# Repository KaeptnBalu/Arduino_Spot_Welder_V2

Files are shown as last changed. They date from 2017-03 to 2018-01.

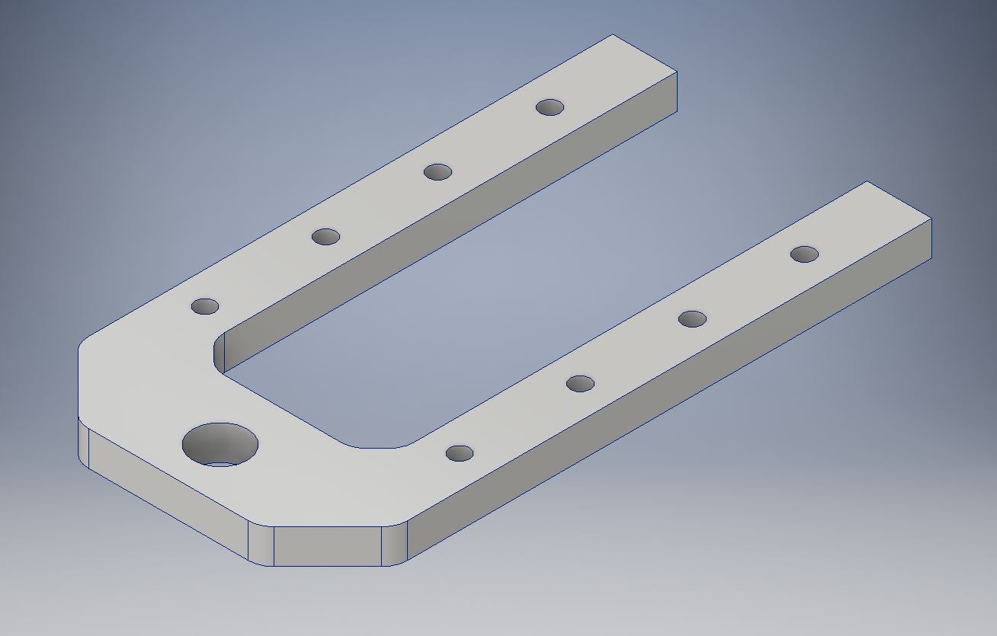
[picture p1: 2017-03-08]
Parts/Aluminum_Parts/Part1_new.JPG

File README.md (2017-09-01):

# Arduino_Spot_Welder_V2

This is the older V2 Version of the Arduino Spot Welder. The new V3 can be found here https://github.com/KaeptnBalu/Arduino_Spot_Welder_V3 The previous V1 can be found here https://github.com/KaeptnBalu/Arduino_Spot_Welder

An Arduino based Spot Welder for battery welding http://www.instructables.com/id/DIY-Arduino-Battery-Spot-Welder/ <br>
Build Video: https://www.youtube.com/watch?v=4qOaeutVR8I

3D prinable cases: 
- https://www.thingiverse.com/thing:2488481   (Thanks to Neil Paisnel)
- https://www.thingiverse.com/thing:2346476   (Thanks to AugustRetroDoom)

Improvements in the V2:

    - only one mosfet driver instead of four
    - changed electrolytic capacitor to film capacitor
    - capacitors closer to the mosfet driver
    - wider pcb traces for high current paths
    - added gate resistors for the mosfets
    - aluminum u-shaped part for the mosfet board (much easier to assemble)
    - general pcb layout improvements
    - pcb is now designed in KiCad (more open source than Eagle)
    
 Improvements in the V2.2:

    - Mosfet PCB now with 2oz copper layer and wider traces 
    which connect the high current carrying mosfet legs to the u-shaped aluminum part
    - little bit bigger mounting holes for u-shaped aluminum piece (2.6mm instead of 2.5mm)
    - "AutoPulse" feature, which automatically activates a pulse after a 2 second delay 
    when both welding tips touch the nickel strip (thanks to Petr Zverina for the idea)

This Spot Welder can be used to weld 18650 batteries. It needs a 7-12V power source (12V recommended) and uses a 12V car battery as welding current supply. Typically one 45Ah battery delivers enough current to get good welds with 0.15mm nickel strips. For thicker nickel strips maybe you will need bigger battery or two in paralell.

The Welder generates a double pulse, where the first one is 1/8 of the time of the second one. Pulse time of second pulse is adjustable by the potentiometer and displayed on the screen in mS so you can exactly adjust the time. Its adjustable from 1 ... 90 mS.

If you want to download the project click on "clone or download" on this page. Downloading single files sometimes seems to cause some files to be corrupted while downloading.

You can get parts to build your own Spot Welder or prebuilt kits at https://malectrics.eu/

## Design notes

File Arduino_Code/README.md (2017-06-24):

The code for the Spot welder V2 or V2.1 is the arduino_spot_welder.ino . The code for the new V2.2 PCBs with "AutoPulse" feature is the Arduino_Spot_Welder_V2.2.ino . Only use the new V2.2 code if you have the new V2.2 PCBs or if you upgraded your old Spot Welder with the necessary parts. 

If you built the spot welder yourself but it doesn't work, you can use the TEST_MODE_Arduino_Spot_Welder.ino to find the error. DO NOT CONNECT THE WELDING WIRES WHEN USING THIS CODE ! With the test code pushing the foot switch turns the mosfets permanent on. This way you can measure all the voltages with a normal multimeter. For example you can check:

- if all mosfet gates get the full voltage when they are on. They should have almost the voltage of your power supply.
- if the Arduino outputs a high signal (5V) to the mosfet drivers (Arduino Pin D5, Mosfet Driver Pin 2)
- if the LED gets a high signal (5V)

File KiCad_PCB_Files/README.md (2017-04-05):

The spot welder is made of two boards which are stacked on top of each other.
One board contains all the logic and low power electronic components and the other one contains the Mosfets.

The gerber files are made to be used at pcbway.com 
You can support me by registering through this link http://www.pcbway.com/setinvite.aspx?inviteid=12824
This way you get a 5$ coupon for your order and i get some percent discount at the shop for upcoming projects.

As the Gerber Files you can use the Spot_Welder_V2_Gerber.zip or the latest Spot_Welder_V2.1_Gerber.zip which have both boards combined to one big board. 
You have to cut this in half at home to get the two single boards.

To download the files please download the complete project by clicking on the "clone or download" button on the projects main page (https://github.com/KaeptnBalu/Arduino_Spot_Welder_V2)
Downloading by right click and "save as" does seem to cause problems.

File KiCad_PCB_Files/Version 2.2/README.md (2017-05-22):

Improvements in Version 2.2

- Mosfet PCB now with 2oz copper layer and wider traces which connect the high current carrying mosfet legs to the u-shaped aluminum part
- little bit bigger mounting holes for u-shaped aluminum piece (2.6mm instead of 2.5mm)
- "AutoPulse" feature, which automatically activates a pulse after a 2 second delay when both welding tips touch the nickel strip (thanks to Petr Zverina for the idea)

The mosfet pcb update was done because some users who tryed welding with more than 1000A current reported that the pcb traces got damaged by the high current. Now it should be more resistant even to these very high currents.

The new "AutoPulse" feature only needs 5 small additional parts on the pcb. (470 Ohm resistor, 620 Ohm resistor, z-diode 4,3V 0,5w, 2,54mm jumper, 2 pin 2,54mm male header). Resistor R13 does not need to be populated. It was meant as a pull down resistor, but after looking close to the schematic i realised R14 + R15 already do the pull down to GND.

To activate the "AutoPulse" feature simply plug a jumper on the male 2 pin header named "Auto_Pulse" which connects the two pins.

You can get the new V2.2 PCB Sets here: https://malectrics.eu/

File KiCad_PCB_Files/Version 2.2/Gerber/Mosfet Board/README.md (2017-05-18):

Gerber files to order the Mosfet Board at a pcb manufacturer

NOTE:
order the mosfet board with 2oz copper to make it able to handle welding currents of more than 1000A

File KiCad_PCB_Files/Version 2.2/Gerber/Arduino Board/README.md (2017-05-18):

Gerber Files to order the Arduino Board at a pcb manufacturer

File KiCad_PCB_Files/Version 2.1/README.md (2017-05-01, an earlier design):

These are the KICAD PCB Files for version 2.1 of the Arduino Spot Welder

Updates in V2.1:

- moved gnd_con text to bottom side
- moved mosfets pads 1mm to board outside
- larger smd pads for the led
- larger pin header pads
- capacitor 0,1µF and shottky diode now smd parts

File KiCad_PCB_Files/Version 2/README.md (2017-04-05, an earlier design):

These are the KICAD pcb files for the Arduino Spot Welder version 2

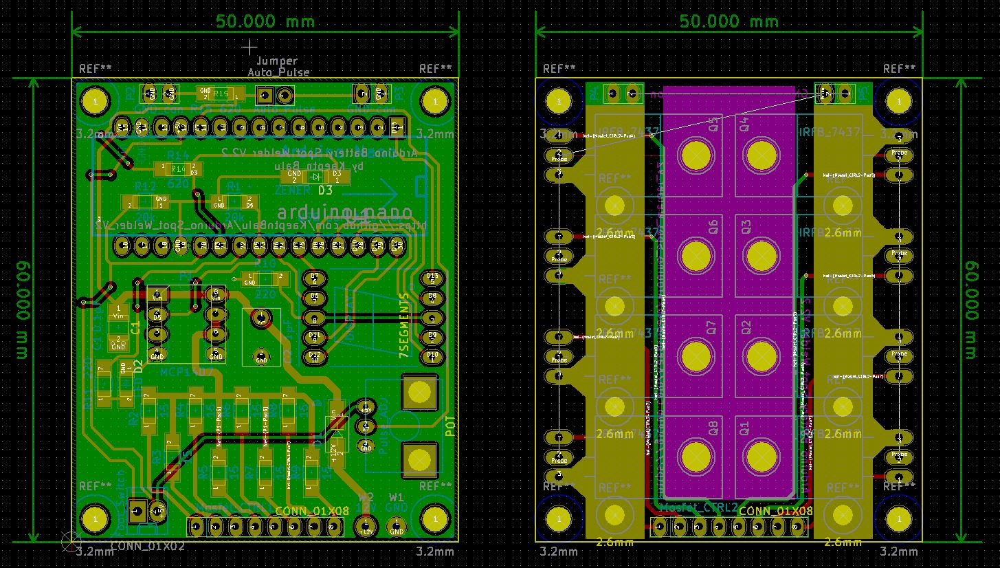
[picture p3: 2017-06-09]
KiCad_PCB_Files/Version 2.2/Pictures/Gerber_PCB.JPG

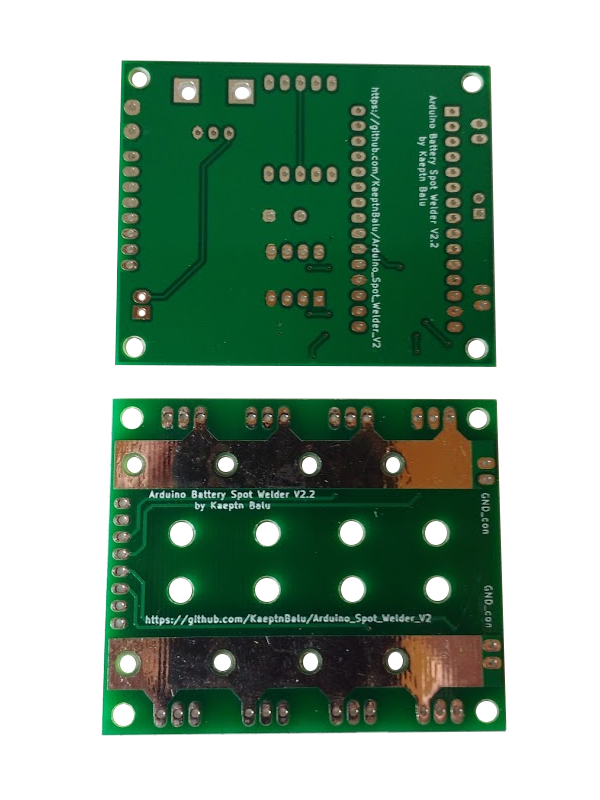
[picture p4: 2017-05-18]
KiCad_PCB_Files/Version 2.2/Pictures/PCB_Set_V2.2_Back.png

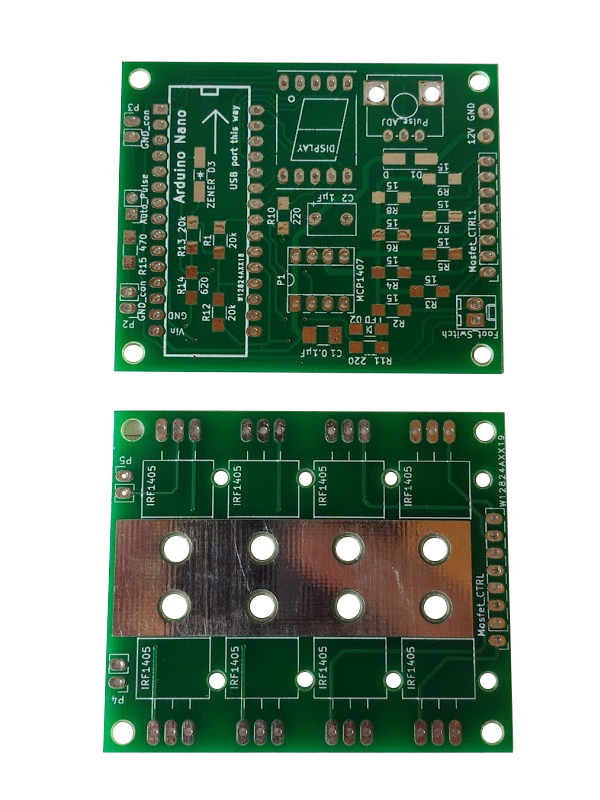
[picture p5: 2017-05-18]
KiCad_PCB_Files/Version 2.2/Pictures/PCB_Set_V2.2_Front.png

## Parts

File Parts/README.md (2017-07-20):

These are the parts you need to buy for building the Spot welder.
With the Reichelt.de or Mouser.com Shop Links you can directly ad all parts to your shopping cart.
For a complete parts list take a look at the BOM files.

Parts not orderd from Reichelt.de:

- 1x Arduino Nano 

Parts I bought at the local hardware store:
- 1x piece of 16x70mm aluminium about 3 or 4mm thick
- Some 16mm² cable and short piece of thick solid copper wire for the probes tips  

Optional:
Diodes to protect the Mosfets from high voltage spikes. (already included in the Mouser.com shopping cart)
- Schottky: VS-100BGQ015 Mouser.com Part: 844-100BGQ015
- TVS: 5KP13A-E3/54 Mouser.com Part: 625-5KP13A-E3

More info on the diodes: https://www.instructables.com/id/DIY-Arduino-Battery-Spot-Welder/step4/Adding-Protection-Diodes-optional/

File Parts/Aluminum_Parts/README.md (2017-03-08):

Use the PDF template to cut the aluminum pieces from 3-4mm material.

The u-shaped piece is optional. You can either solder the thick wire bend to an u-shape directly to the pcb as before or cut this aluminum piece and screw it with m2 screws to the pcb.

You can also take a look at the 3d and dxf drawings to manufacture the aluminum parts with a cnc or something else.

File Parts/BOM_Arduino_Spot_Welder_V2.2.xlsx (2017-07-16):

 |  |  | Reichelt.de Parts |  |  | Complete Shopping Card Link (https://www.reichelt.de/my/1326082)
Quantity | PCB Onprint | Name | Reichelt.de Part Number | Price/piece | Price all | Reichelt.de Link
8 | IRFB_7437 | Mosfet IRFB 7437 40V 250A | IRFB 7437 | 1.20 € | 9.60 € | https://www.reichelt.de/Transistors-IRFB-IRFI-/IRFB-7437/3/index.html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
1 | P1 MCP1407 | Mosfet Driver MCP1407-E/P | MCP 1407-E/P |  | 0.99 € | https://www.reichelt.de/ICs-MCP-1-2-/MCP-1407-E-P/3/index.html?ACTION=3&GROUPID=5471&ARTICLE=90039&OFFSET=75
1 | Pulse_ADJ | Poti 6mm Linear 50K | RK09K113-LIN50K |  | 0.76 € | https://www.reichelt.de/6mm-Potis-mono/RK09K113-LIN50K/3/index.html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
1 | Display | 7 Segment Display | SC 56-11 RT |  | 0.90 € | https://www.reichelt.de/Siebensegment-Anzeigen/SC-56-11-RT/3/index.html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
3 | Mosfet_CTRL, P4, P5, Arduino Nano | 1x20pol female header | BL 1X20G8 2,54 | 0.27 € | 0.81 € | https://www.reichelt.de/Buchsenleisten/BL-1X20G8-2-54/3/index.html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
1 | P2, P3, Auto_Pulse, Mosfet_ CTRL1 | 1x36pol male header | SL 1X36G 2,54 |  | 0.17 € | https://www.reichelt.de/Stiftleisten/SL-1X36G-2-54/3/index.html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
1 | Foot_Switch | PCB connector set 2pin | PS 25/2G WS |  | 0.26 € | https://www.reichelt.de/Platinen-Steckverbinder/PS-25-2G-WS/3/index.html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
1 | Auto_Pulse | Jumper 2,54mm | JUMPER 2,54GL SW |  | 0.02 € | https://www.reichelt.de/Stiftleisten/JUMPER-2-54GL-SW/3/index.html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
1 | P1 MCP1407 | IC socket 8 pole | GS 8 |  | 0.04 € | https://www.reichelt.de/IC-Sockel/GS-8/3/index.html?ACTION=3&GROUPID=3215&ARTICLE=8230&START=0&OFFSET=1000
1 | D1 | SMD-Schottky 60V 1A | SS 16 |  | 0.08 € | https://www.reichelt.de/SB-SKE-4F-Dioden/SS-16/3/index.html?ACTION=3&GROUPID=2991&ARTICLE=146605&OFFSET=75
1 | C2 | film capacitor 1,5 µF RM5 | MKS2-63 1,5µ |  | 0.32 € | https://www.reichelt.de/MKS-2/MKS2-63-1-5-/3/index.html?ACTION=3&GROUPID=7169&ARTICLE=12348&OFFSET=75
1 | C1 | ceramic capacitor 100nF SMD | X7R 1210 CG 100N |  | 0.07 € | https://www.reichelt.de/Vielschicht-SMD-G1210/X7R-1210-CG-100N/3/index.html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
1 | Zener D3 | SMD Zener diode 4,3V 0,5W | SMD ZF 4,3 |  | 0.04 € | https://www.reichelt.de/Diodes-SMD-Z-Mini-Melf/SMD-ZF-4-3/3/index.html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
2 | R10, R11 | Resistor 1206 SMD 220 Ohm | RND 1206 1 220 | 0.02 € | 0.04 € | https://www.reichelt.de/SMD-1206-von-0-bis-910-Ohm/RND-1206-1-220/3/index.html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
1 | R15 | Resistor 1206 SMD 470 Ohm | SMD 1/4W 470 |  | 0.03 € | https://www.reichelt.de/SMD-1206-von-0-bis-910-Ohm/SMD-1-4W-470/3/index.html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
1 | R14 | Resistor 1206 SMD 620 Ohm | RND 1206 1 620 |  | 0.02 € | https://www.reichelt.de/SMD-1206-von-0-bis-910-Ohm/RND-1206-1-620/3/index.html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
2 | R1, R12 | Resistor 1206 SMD 20 kOhm | RND 1206 1 20K | 0.02 | 0.04 € | https://www.reichelt.de/SMD-1206-von-1-bis-910-kOhm/RND-1206-1-20K/3/index.html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
8 | R2, R3, R4, R5, R6, R7, R8, R9 | Resistor 1206 SMD 15 Ohm | RND 1206 1 15 | 0.02 | 0.16 € | https://www.reichelt.de/SMD-1206-von-0-bis-910-Ohm/RND-1206-1-15/3/index.html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
1 | LED D2 | LED 1206 SMD green | LED EL 1206 GR1 |  | 0.08 € | https://www.reichelt.de/SMD-LEDs-Standard/LED-EL-1206-GR1/3/index.html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
 |  |  | Components Total: |  | 14.43 €
 |  |  | Other Parts
1 |  | Arduino Nano |  |  | 2.00 € | Aliexpress.com
1 |  | Alu 17x70x4mm + 37x70x4mm | see alu_template.pdf (https://github.com/KaeptnBalu/Arduino_Spot_Welder_V2/blob/master/Parts/Aluminum_Parts/alu_template.pdf) |  | 2 € | local hardware Store or https://malectrics.eu/
1 |  | 1,2m 16 mm² flexible cable |  |  | 3 € | e.g. old car starter cable or https://www.schweisshelden.de/schweisskabel-h01n2-d-16-mm2-48129
1 |  | 0,1m 16mm² solid copper wire | for the welding tips |  | 1 € | local hardware store
3 |  | cable lug for 16 mm² |  | 0.6 | 1.80 € | local hardware store or http://www.voelkner.de/products/9287/Ringkabelschuh-16-25mm-6mm-Gelb.html
1 |  | battery clip | for car battery |  | 1.95 € | local hardware store or http://www.voelkner.de/products/80594/Batterieklemme-Gerade-Plus-Minus.html
1 |  | PCB | from malectrics.eu |  | 5.80 € | https://malectrics.eu/
1 |  | Schottky Diode: VS-100BGQ015 | Optional Part |  | 4.57 € | http://www.mouser.de/ProductDetail/Vishay-Semiconductors/VS-100BGQ015/
1 |  | TVS Diode : 5KP13A-E3/54 | Optional Part |  | 2.01 € | http://www.mouser.de/ProductDetail/Vishay-Semiconductors/5KP13A-E3-54/
 |  |  | Other Parts Total: |  | 24.13 €
 |  |  | TOTAL COST |  | 38.56 €

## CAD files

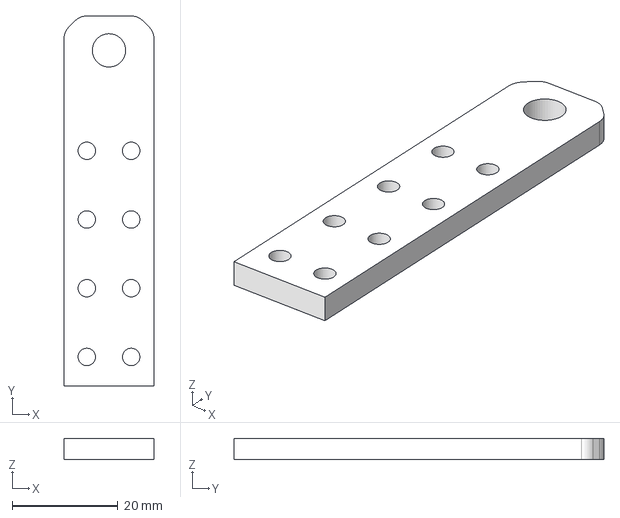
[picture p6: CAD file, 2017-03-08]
Parts/Aluminum_Parts/Part2_new.stp
17.0 x 70.0 x 4.00 mm

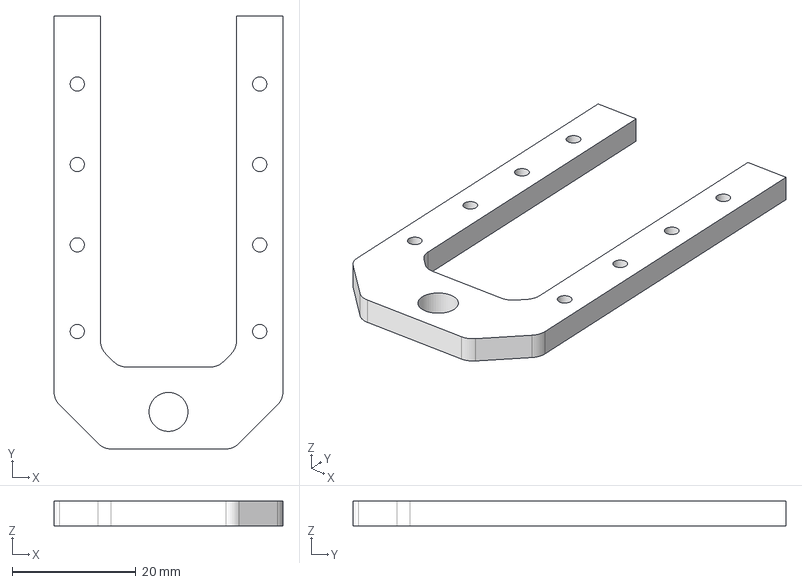
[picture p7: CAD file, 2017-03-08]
Parts/Aluminum_Parts/Part1_new.stp
37.0 x 70.0 x 4.00 mm

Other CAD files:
Parts/Aluminum_Parts/Part1_new.dxf
Parts/Aluminum_Parts/Part1_new.ipt
Parts/Aluminum_Parts/Part2_new.dxf
Parts/Aluminum_Parts/Part2_new.ipt

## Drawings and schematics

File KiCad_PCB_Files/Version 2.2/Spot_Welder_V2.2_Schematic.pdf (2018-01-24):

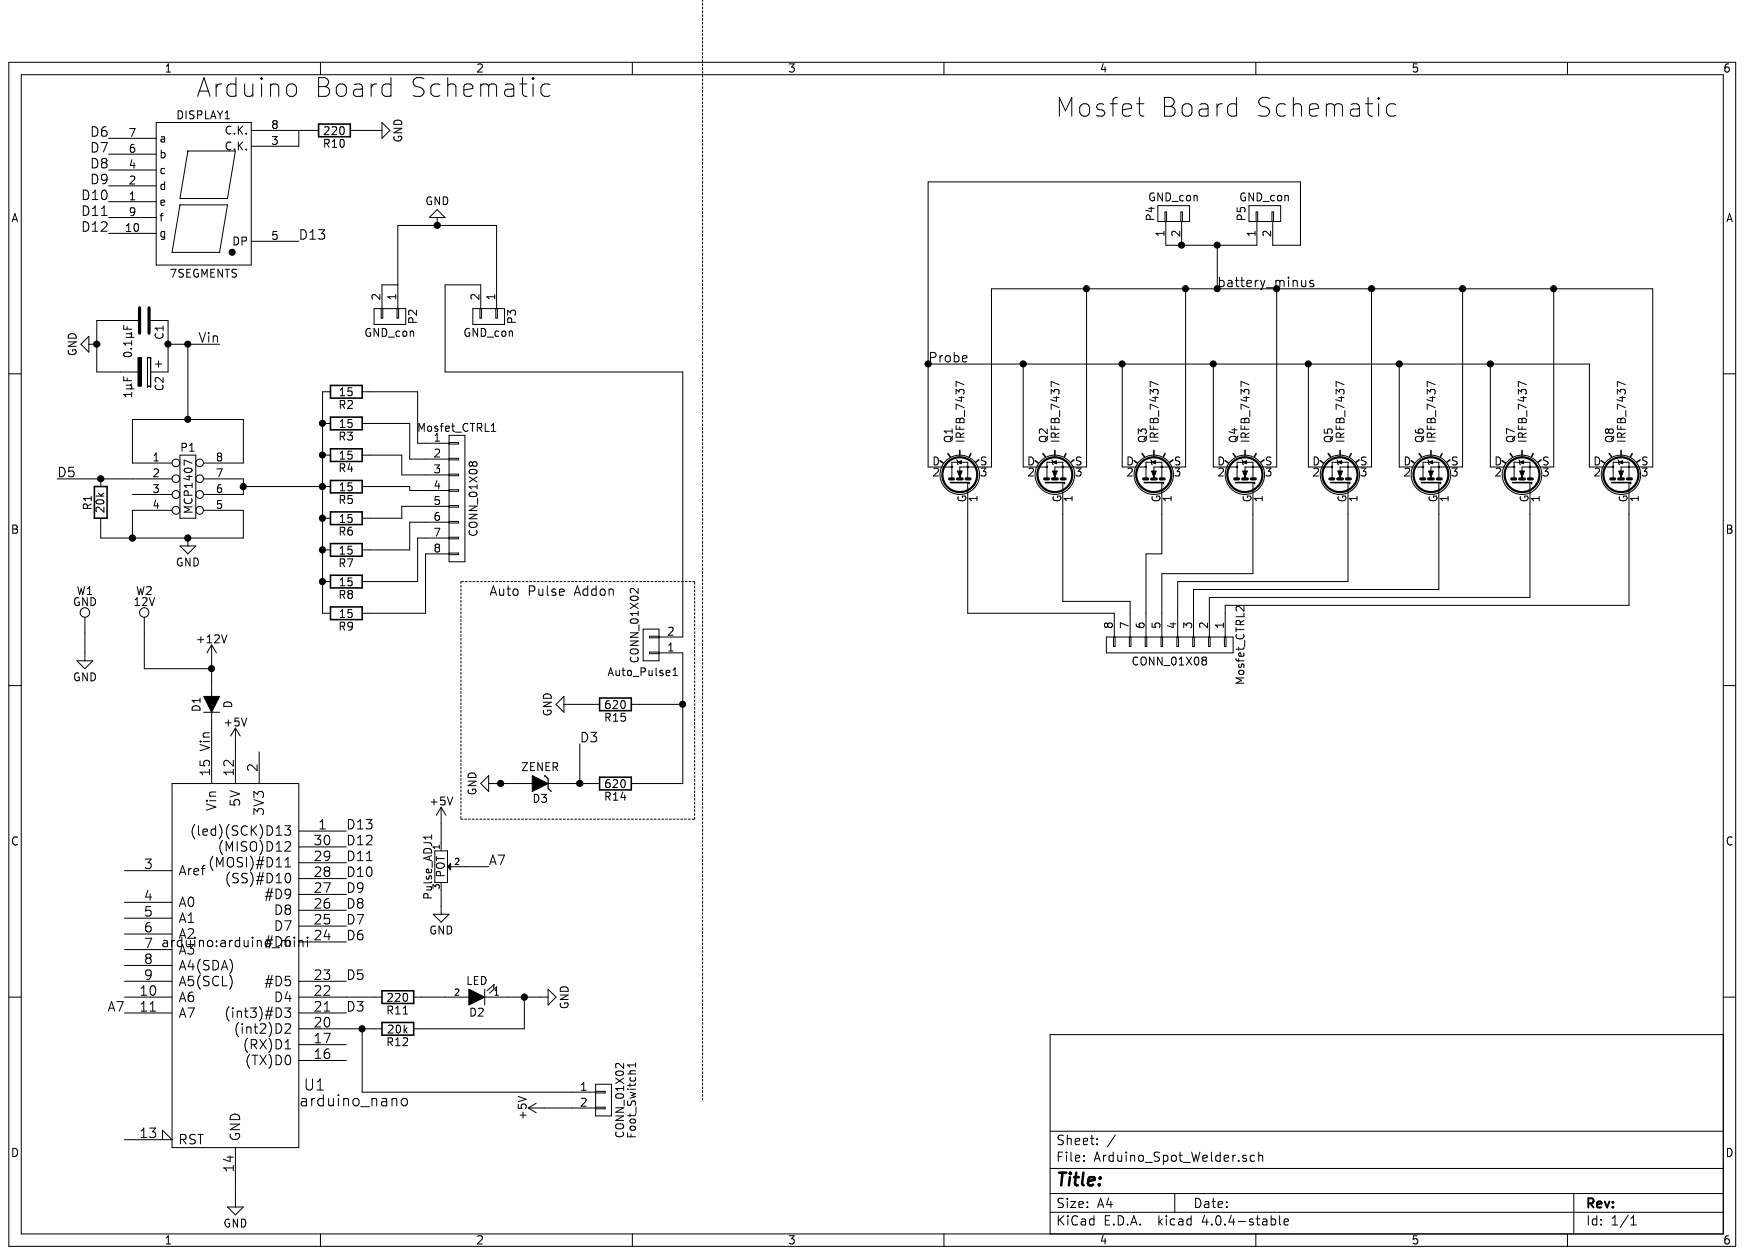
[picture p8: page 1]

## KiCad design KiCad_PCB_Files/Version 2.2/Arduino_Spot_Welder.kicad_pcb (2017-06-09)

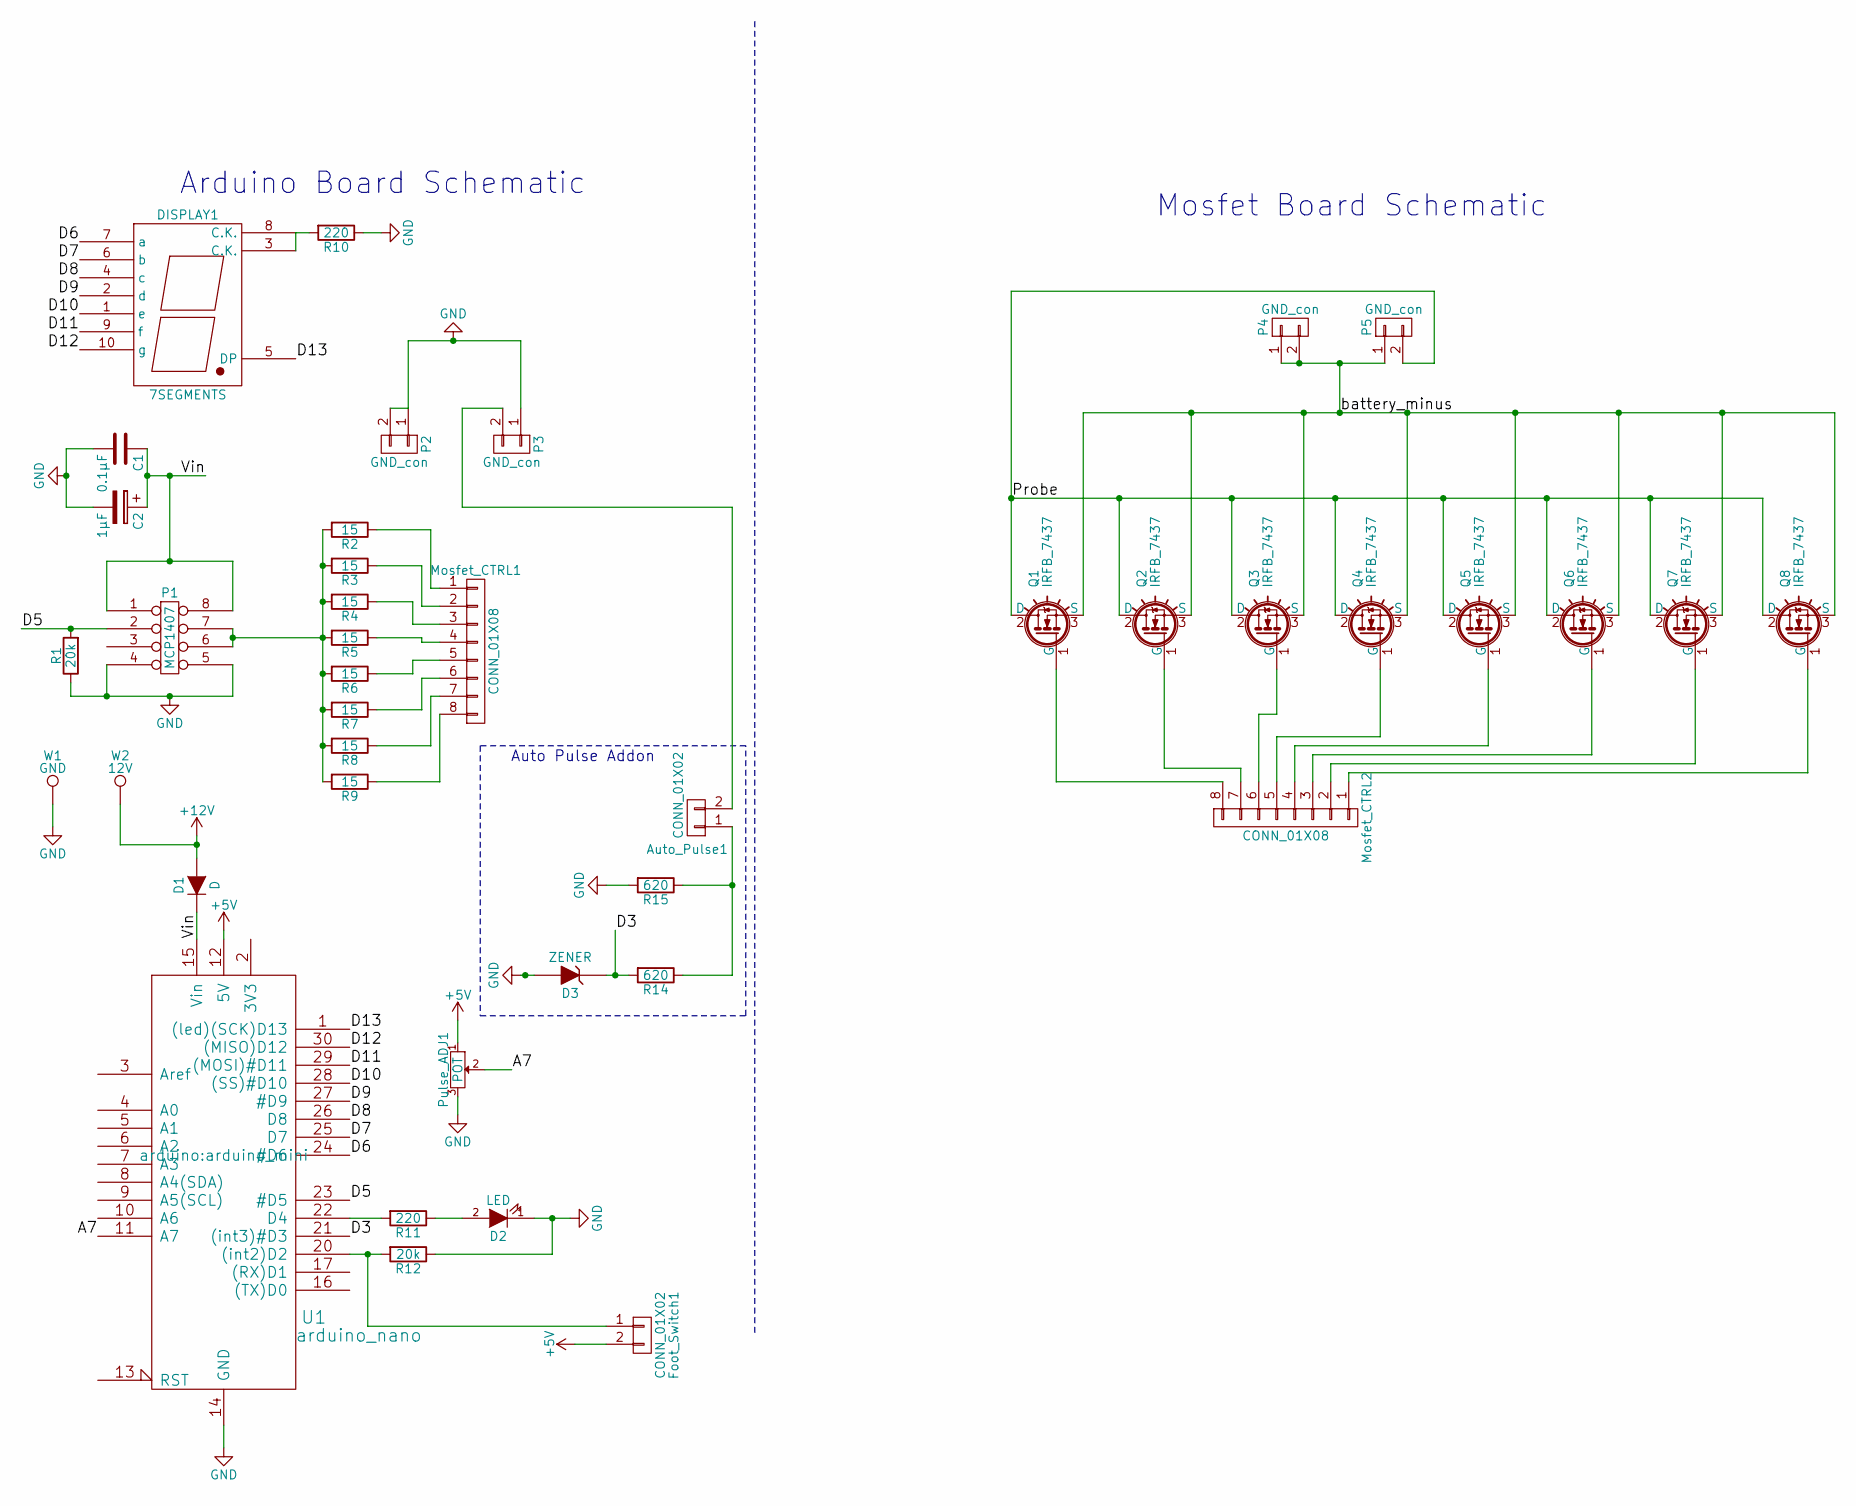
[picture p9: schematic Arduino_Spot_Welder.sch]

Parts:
Auto_Pulse1: CONN_01X02; Pin_Header_Straight_1x02_Pitch2.54mm
C1: 0.1µF; C_1210_HandSoldering
C2: 1µF; C_Disc_D7.5mm_W5.0mm_P5.00mm
D1: D; D_SMA_Handsoldering
D2: LED; R_1206_HandSoldering
D3: ZENER; D_MiniMELF_Handsoldering
DISPLAY1: 7SEGMENTS; 7SegmentLED_LTS6760_LTS6780
Foot_Switch1: CONN_01X02; Molex_KK-6410-02_02x2.54mm_Straight
Mosfet_CTRL1, Mosfet_CTRL2: CONN_01X08; Pin_Header_Straight_1x08_Pitch2.54mm_Large_Pads
P1: MCP1407; DIP-8_W7.62mm_Socket_LongPads
P2, P3, P4, P5: GND_con; Pin_Header_Straight_1x02_Pitch2.54mm
Pulse_ADJ1: POT; RK09K1130A5R
Q1, Q2, Q3, Q4, Q5, Q6, Q7, Q8: IRFB_7437; TO-220__long_Neutral123_Horizontal_LargePads
R1, R12: 20k; R_1206_HandSoldering
R2, R3, R4, R5, R6, R7, R8, R9: 15; R_1206_HandSoldering
R10, R11: 220; R_1206_HandSoldering
R14, R15: 620; R_1206_HandSoldering
U1: arduino_nano; arduino_mini
W1: GND; SolderWirePad_single_1mmDrill
W2: 12V; SolderWirePad_single_1mmDrill

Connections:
+5V: Foot_Switch1.2, Pulse_ADJ1.1, U1.12 (5V); also elsewhere on the board
+12V: D1.2 (A), W2.1
/A7: Pulse_ADJ1.2, U1.11 (A7); also elsewhere on the board
/D3: D3.1 (K), R14.2, U1.21 ((int3)#D3)
/D5: P1.2, R1.2, U1.23 (#D5)
/D6: DISPLAY1.7 (a), U1.24 (#D6); also elsewhere on the board
/D7: DISPLAY1.6 (b), U1.25 (D7); also elsewhere on the board
/D8: DISPLAY1.4 (c), U1.26 (D8); also elsewhere on the board
/D9: DISPLAY1.2 (d), U1.27 (#D9); also elsewhere on the board
/D10: DISPLAY1.1 (e), U1.28 ((SS)#D10); also elsewhere on the board
/D11: DISPLAY1.9 (f), U1.29 ((MOSI)#D11); also elsewhere on the board
/D12: DISPLAY1.10 (g), U1.30 ((MISO)D12); also elsewhere on the board
/D13: DISPLAY1.5 (DP), U1.1 ((led)(SCK)D13); also elsewhere on the board
/Probe: P5.2, Q1.2 (D), Q2.2 (D), Q3.2 (D), Q4.2 (D), Q5.2 (D), Q6.2 (D), Q7.2 (D), Q8.2 (D)
/Vin: C1.1, C2.1, D1.1 (K), P1.1, P1.8, U1.15 (Vin)
/battery_minus: P4.1, P4.2, P5.1, Q1.3 (S), Q2.3 (S), Q3.3 (S), Q4.3 (S), Q5.3 (S), Q6.3 (S), Q7.3 (S), Q8.3 (S)
GND: C1.2, C2.2, D2.1 (K), D3.2 (A), P1.4, P1.5, P2.1, P2.2, P3.1, Pulse_ADJ1.3, R1.1, R10.1, R12.1, R15.2, U1.14 (GND), U1.19 (GND), W1.1; also elsewhere on the board
unnamed 17: Auto_Pulse1.1, R14.1, R15.1; also elsewhere on the board
unnamed 18: Auto_Pulse1.2, P3.2; also elsewhere on the board
unnamed: D2.2 (A), R11.1
unnamed 20: DISPLAY1.3 (C.K.), DISPLAY1.8 (C.K.), R10.2; also elsewhere on the board
unnamed 21: Foot_Switch1.1, R12.2, U1.20 ((int2)D2); also elsewhere on the board
unnamed: Mosfet_CTRL1.1, R2.1
unnamed: Mosfet_CTRL1.2, R3.1
unnamed: Mosfet_CTRL1.3, R4.1
unnamed: Mosfet_CTRL1.4, R5.1
unnamed: Mosfet_CTRL1.5, R6.1
unnamed: Mosfet_CTRL1.6, R7.1
unnamed: Mosfet_CTRL1.7, R8.1
unnamed: Mosfet_CTRL1.8, R9.1
unnamed: Mosfet_CTRL2.1, Q8.1 (G)
unnamed: Mosfet_CTRL2.2, Q7.1 (G)
unnamed: Mosfet_CTRL2.3, Q6.1 (G)
unnamed: Mosfet_CTRL2.4, Q5.1 (G)
unnamed: Mosfet_CTRL2.5, Q4.1 (G)
unnamed: Mosfet_CTRL2.6, Q3.1 (G)
unnamed: Mosfet_CTRL2.7, Q2.1 (G)
unnamed: Mosfet_CTRL2.8, Q1.1 (G)
unnamed: P1.6, P1.7, R2.2, R3.2, R4.2, R5.2, R6.2, R7.2, R8.2, R9.2
unnamed: R11.2, U1.22 (D4)

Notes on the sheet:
Arduino Board Schematic
Mosfet Board Schematic
Auto Pulse Addon

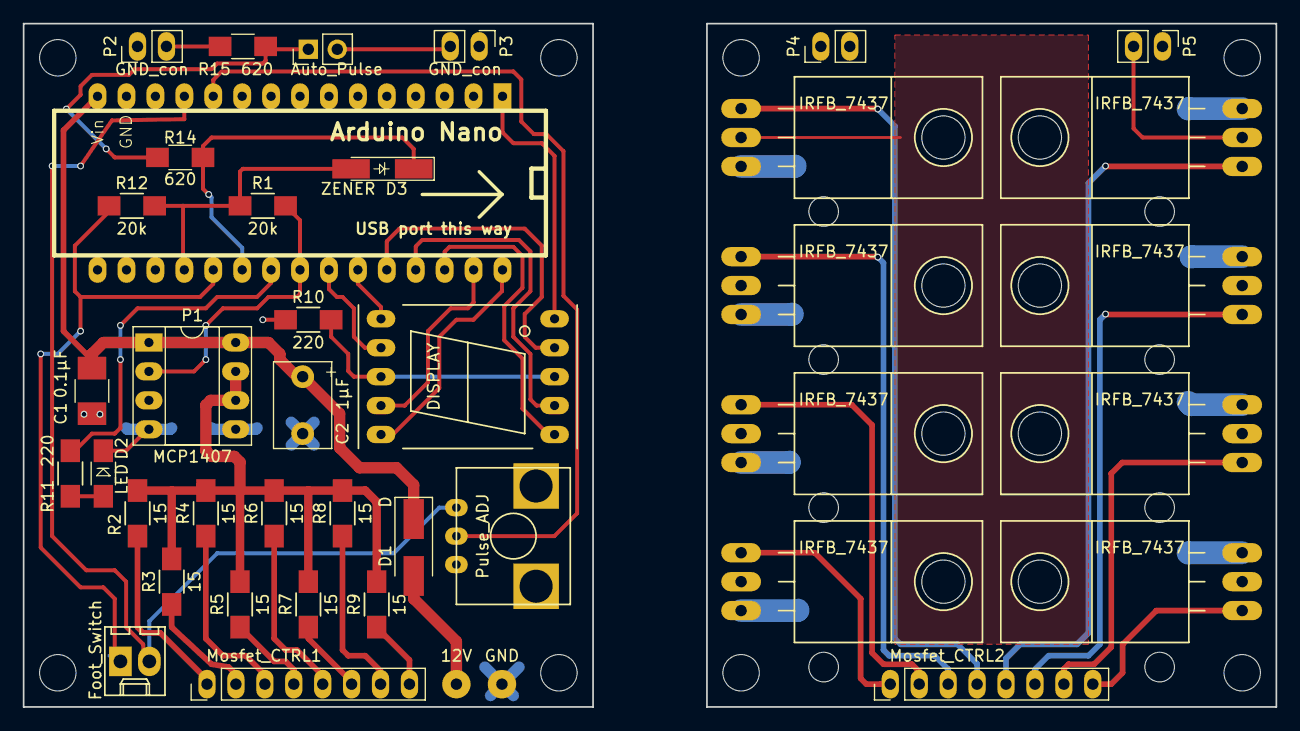
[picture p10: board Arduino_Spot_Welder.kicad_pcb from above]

Board: 2 copper layers, 110.0 x 60.0 mm, 41 parts (0 on the bottom side), 40 nets.

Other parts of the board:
Auto_Pulse: Jumper; Pin_Header_Straight_1x02_Pitch2.54mm
DISPLAY: 7SEGMENTS; 7SegmentLED_LTS6760_LTS6780
Foot_Switch: CONN_01X02; Molex_KK-6410-02_02x2.54mm_Straight
Pulse_ADJ: POT; RK09K1130A5R

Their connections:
+5V: Foot_Switch.2, Pulse_ADJ.1; also elsewhere on the board
/A7: Pulse_ADJ.2; also elsewhere on the board
/D6: DISPLAY.7; also elsewhere on the board
/D7: DISPLAY.6; also elsewhere on the board
/D8: DISPLAY.4; also elsewhere on the board
/D9: DISPLAY.2; also elsewhere on the board
/D10: DISPLAY.1; also elsewhere on the board
/D11: DISPLAY.9; also elsewhere on the board
/D12: DISPLAY.10; also elsewhere on the board
/D13: DISPLAY.5; also elsewhere on the board
GND: Pulse_ADJ.3; also elsewhere on the board
unnamed 17: Auto_Pulse.1; also elsewhere on the board
unnamed 18: Auto_Pulse.2; also elsewhere on the board
unnamed 20: DISPLAY.3, DISPLAY.8; also elsewhere on the board
unnamed 21: Foot_Switch.1; also elsewhere on the board

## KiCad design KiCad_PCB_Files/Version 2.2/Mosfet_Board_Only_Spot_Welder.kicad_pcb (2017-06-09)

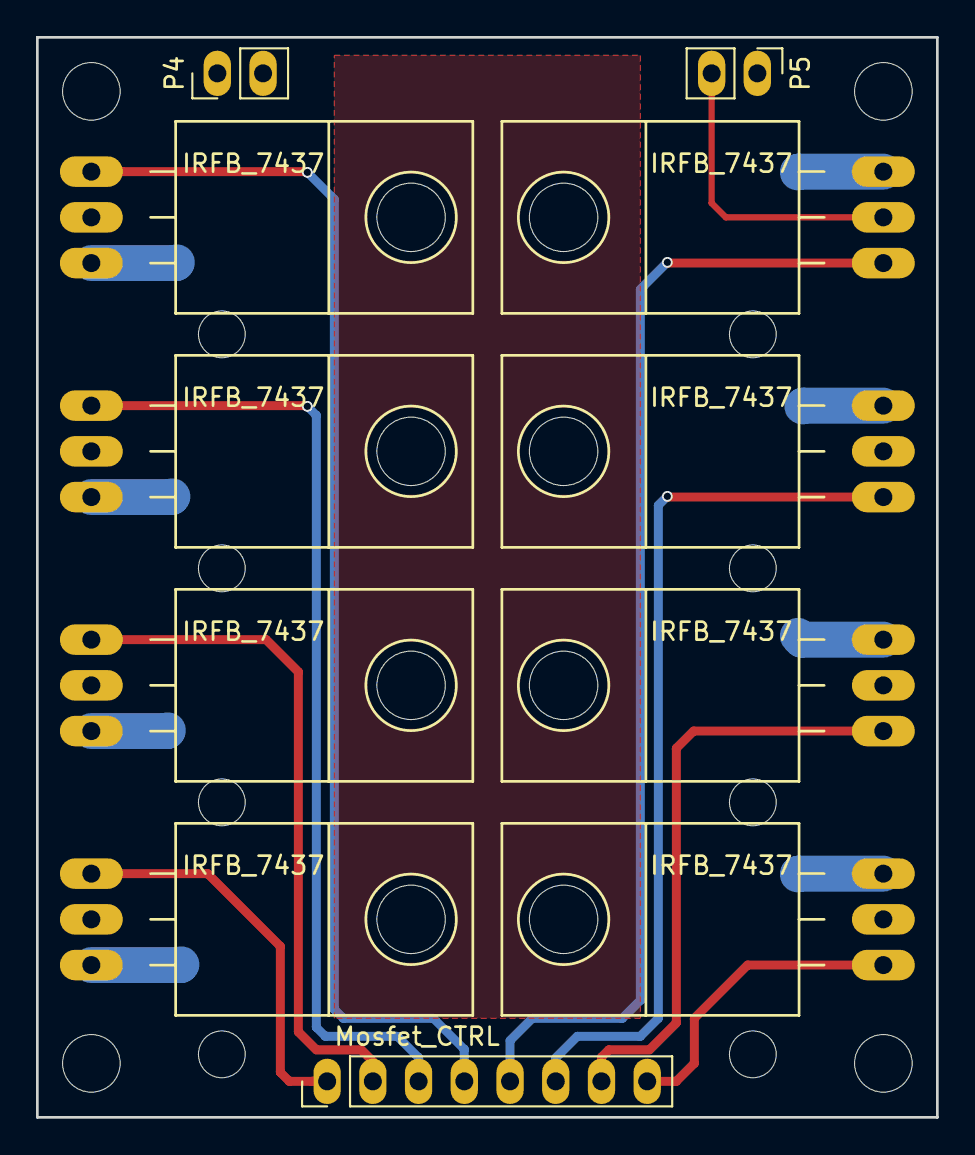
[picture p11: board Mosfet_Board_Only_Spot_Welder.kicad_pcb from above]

Board: 2 copper layers, 50.0 x 60.0 mm, 11 parts (0 on the bottom side), 10 nets.

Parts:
Mosfet_CTRL: CONN_01X08; Pin_Header_Straight_1x08_Pitch2.54mm_Large_Pads
P4, P5: GND_con; Pin_Header_Straight_1x02_Pitch2.54mm
Q1, Q2, Q3, Q4, Q5, Q6, Q7, Q8: IRFB_7437; TO-220__long_Neutral123_Horizontal_LargePads

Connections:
/Probe: P5.2, Q1.2, Q2.2, Q3.2, Q4.2, Q5.2, Q6.2, Q7.2, Q8.2
/battery_minus: P4.1, P4.2, P5.1, Q1.3, Q2.3, Q3.3, Q4.3, Q5.3, Q6.3, Q7.3, Q8.3
unnamed: Mosfet_CTRL.1, Q8.1
unnamed: Mosfet_CTRL.2, Q7.1
unnamed: Mosfet_CTRL.3, Q6.1
unnamed: Mosfet_CTRL.4, Q5.1
unnamed: Mosfet_CTRL.5, Q4.1
unnamed: Mosfet_CTRL.6, Q3.1
unnamed: Mosfet_CTRL.7, Q2.1
unnamed: Mosfet_CTRL.8, Q1.1

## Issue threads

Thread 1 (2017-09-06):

Possible to use V2.1 with a LiPo-Battery?

seewaldjan, 2017-09-06:
Is it possible to use the V2.1-PCB with a LiPo-Battery 11,1V 30C 5000mAh? It would generate 5Ah*30C=150Amps of current. Is that enough? Do I need some additional circuit protection?

KaeptnBalu, 2017-09-06:
Hi,

On V2.1 i would recommend to install the Diode Set. https://malectrics.eu/product/arduino-spot-welder-diode-set/

Using the Lipo battery should work. Maybe you need to use a bit higher pulse time as with a car battery.

The question is if the Lipo battery will survive this treatment. I use a Turnigy Nano Tech 5000mAh 65-130C 3s Lipo.

This has now abou 1500 welds on it with no problem.

But i tested a old hacker 5000mAh 3s 25C lipo before and it got "puffy" after a few welds.

Greetings,

Marc

Gesendet: Mittwoch, 06. September 2017 um 16:07 Uhr
Von: Jan <notifications@github.com>
An: KaeptnBalu/Arduino_Spot_Welder_V2 <Arduino_Spot_Welder_V2@noreply.github.com>
Cc: Subscribed <subscribed@noreply.github.com>
Betreff: [KaeptnBalu/Arduino_Spot_Welder_V2] Possible to use V2.1 with a LiPo-Battery? (#1)

Is it possible to use the V2.1-PCB with a LiPo-Battery 11,1V 30C 5000mAh? It would generate 5Ah*30C=150Amps of current. Is that enough? Do I need some additional circuit protection?

—
You are receiving this because you are subscribed to this thread.
Reply to this email directly, view it on GitHub, or mute the thread.

seewaldjan, 2017-09-06:
Thank you, I will try that out! So I don't need a fuse like in V3? I already have the Diode set, if that is sufficient, than I will test it the next days. Maybe the LiPo get puffy, but I will see it.

KaeptnBalu, 2017-09-06:
Hi,

If you are carefull while welding you dont need the fuse for the unit to work properly.

Its only a safety addon if something goes wrong.

Gesendet: Mittwoch, 06. September 2017 um 18:19 Uhr
Von: Jan <notifications@github.com>
An: KaeptnBalu/Arduino_Spot_Welder_V2 <Arduino_Spot_Welder_V2@noreply.github.com>
Cc: Marc <marc328@gmx.de>, Comment <comment@noreply.github.com>
Betreff: Re: [KaeptnBalu/Arduino_Spot_Welder_V2] Possible to use V2.1 with a LiPo-Battery? (#1)

Thank you, I will try that out! So I don't need a fuse like in V3? I already have the Diode set, if that is sufficient, than I will test it the next days. Maybe the LiPo get puffy, but I will see it.

—
You are receiving this because you commented.
Reply to this email directly, view it on GitHub, or mute the thread.

seewaldjan, 2017-09-14:
me again - is it possible to use an electrolytic capacitor with 1µF instead of an film capacitor

KaeptnBalu, 2017-09-14:
Yes it should Work. Just make Sure top get the polarity right.Am 14.09.2017 8:52 nachm. schrieb Jan <notifications@github.com>:me again - is it possible to use an electrolytic capacitor with 1µF instead of an film capacitor

—You are receiving this because you commented.Reply to this email directly, view it on GitHub, or mute the thread.

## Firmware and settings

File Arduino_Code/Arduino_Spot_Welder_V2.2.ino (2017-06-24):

// Arduino Battery Spot Welder V2.2
// Project Page: http://www.instructables.com/id/DIY-Arduino-Battery-Spot-Welder/

int max_pulse_time = 90; // Sets the maximum pulse time to 90mS (do not use higher than 99 because the display only works up to 99)
int autopulse_delay = 2000; // Delay until the pulse is activated after both welding tips touch the nickel strip (2000 = 2 seconds) 
int mosfetPin = 5;  // Pin that controls the mosfet drivers
int ledPin = 4;   // Pin to control the status led
int switchPin = 2;  // Pin to trigger a pulse with the foot switch
int autopulsePin = 3;  // Pin to trigger a pulse with a little delay as soon as both welding tips touch the nickel strip
int sensorPin = A7;  // Pin where the potentiometer value is read
int previous_pulse_time; // Previous pulse time so display can skip to ones digit
int pulse_time;   // Variable to store the pulse time
int pulse_short;  // Variable to store the short pulse time
int displayStep = 0; // The step the display function should complete next
unsigned long previousMillis = millis(); // The milliseconds where the timer starts counting from
int tens = 0; // Tens place digit
int ones = 0; // Ones place digit
float pulse_calc = 1023 / max_pulse_time;

// Defines the possible characters to be displayed on the 7-segment display in an array
//            0          1          2          3          4          5          6          7          8          9          .          None       All
byte y[13] = {B11111100, B01100000, B11011010, B11110010, B01100110, B10110110, B10111110, B11100000, B11111110, B11110110, B00000001, B00000000, B11111111}; // Ones
byte z[13] = {B11111100, B00001100, B11011010, B11110010, B01100110, B10110110, B10111110, B11100000, B11111110, B11110110, B00000001, B00000000, B11111111}; // Tens


//-------------------------------------------------------------------------------------------

void setup() {
  pinMode(switchPin, INPUT); // Set switchPin as Input
  pinMode(mosfetPin, OUTPUT); // Set mosfetPin as Output
  pinMode(ledPin, OUTPUT); // Set ledPin as Output
  pinMode(sensorPin, INPUT); // Set sensorPin as Input

  // Set up 7 Segment Pins
  for (int i = 6; i <= 13; i++) // Pins 6-13 are set as Outputs
    pinMode(i, OUTPUT);

  // Light up the led and the display 2 seconds to verify correct placement and function
  digitalWrite(ledPin, HIGH);
  segments(z[12]);
  delay(2000);
  digitalWrite(ledPin, LOW);
  segments(z[11]);
}

//-------------------------------------------------------------------------------------------

void loop() {

  // Read pulse time from analog input
  read_pulse_time();

  // Display time on 7-segment display
  time_display();

  // Impulse activated by switch
  if (digitalRead(switchPin) == HIGH && pulse_time > 0) {
    double_pulse();
    // Wait until switch has been released
    do {
      digitalWrite(mosfetPin, LOW);
      digitalWrite(ledPin, LOW);
    } while (digitalRead(switchPin) == HIGH);
    // Delay before impulse can be triggered again
    delay(500);
  }
  else
  {
    digitalWrite(mosfetPin, LOW);
    digitalWrite(ledPin, LOW);
  }

    // Auto pulse feature (if both welding tips touch the nickel strip the pulse is activated)
    if (digitalRead(autopulsePin) == HIGH && pulse_time > 0) {
      delay(autopulse_delay);
      double_pulse();
    // Wait until switch has been released
    do {
      digitalWrite(mosfetPin, LOW);
      digitalWrite(ledPin, LOW);
    } while (digitalRead(autopulsePin) == HIGH);
    // Delay before impulse can be triggered again
    delay(500);
  }
  else
  {
    digitalWrite(mosfetPin, LOW);
    digitalWrite(ledPin, LOW);
  }  
    
}

//-------------------------------------------------------------------------------------------

void segments(byte n) {
  // controll all 7 Segments

  for (int k = 6; k <= 13; k++) {
    if ((n & B10000000) > 0)
      digitalWrite(k, HIGH);
    else
      digitalWrite(k, LOW);
    n = n << 1;
  }
}

//-------------------------------------------------------------------------------------------

void read_pulse_time() {
  // Read the potentiometer and shift the value to correct the midpoint
  // This allows 20 to be selected without the value having to be exactly 1023
  int sensorValue = analogRead(sensorPin) + pulse_calc/2;

  // Add a small amount of hysteresis
  if ((sensorValue - 3) / pulse_calc > pulse_time) {
    // Makes a pulse of max 20 mS because SensorValue can max become 1023
    pulse_time = sensorValue / pulse_calc;
  }
  if ((sensorValue + 3) / pulse_calc < pulse_time) {
    pulse_time = sensorValue / pulse_calc;
  }
}

//-------------------------------------------------------------------------------------------

void reset_timer() {
  // Set timer to start counting from current time
  previousMillis = millis();
}

//-------------------------------------------------------------------------------------------

bool delay_done(unsigned long delay) {
  // If difference between current time and previous time is more than the delay
  if ((unsigned long)(millis() - previousMillis) >= delay) {
    return true;
  }
  return false;
}

//-------------------------------------------------------------------------------------------

void time_display() { // 7 segment pulse time displaying
  if (pulse_time != previous_pulse_time) {
    previous_pulse_time = pulse_time;

    // Skip to ones digit
    displayStep = 2;
  }

  if (tens == 0) {
    // Skip to ones digit
    displayStep = 2;
  }

  tens = (pulse_time % 100) / 10; // Tens place
  ones = pulse_time % 10; // Ones place

  //delay(500);

  switch (displayStep) {
    // Display tens digit
    case 0:
      // Time to clear display after displaying both digits
      if (delay_done(400)) {
        // Display tens digit
        segments(z[tens]);

        reset_timer();
        displayStep = 1;
      }
      break;

    // Delay after showing tens digit
    case 1:
      if (delay_done(300)) {
        // Clear display
        segments(z[11]);

        displayStep = 2;
      }
      break;

    // Display ones digit
    case 2:
      segments(y[ones]);

      reset_timer();
      displayStep = 3;

      break;

    // Delay after showing ones digit
    case 3:
      if (delay_done(300)) {
        // Clear display
        segments(z[11]);

        reset_timer();
        displayStep = 0;
      }
      break;
  }
}

//-------------------------------------------------------------------------------------------

void double_pulse() {

  pulse_short = (pulse_time / 8); // Impulse with 1/8 the time of pulse_time

  if (pulse_short < 1) // Makes the short pulse at least one millisecond
    pulse_short = 1;

  digitalWrite(ledPin, HIGH);
  digitalWrite(mosfetPin, HIGH);
  delay(pulse_short);
  digitalWrite(mosfetPin, LOW);
  delay(pulse_short);
  digitalWrite(mosfetPin, HIGH);
  delay(pulse_time);
  digitalWrite(mosfetPin, LOW);

  // Keep LED on for extra 50ms
  delay(50);
  digitalWrite(ledPin, LOW);

}

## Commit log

2017-03-08 bill of material
    [BOM_Arduino_Spot_Welder_V2.xlsx]
2017-05-13 updated film capacitor
    [BOM_Arduino_Spot_Welder_V2.1.xlsx, BOM_Arduino_Spot_Welder_V2.xlsx]
2017-06-03 updated mosfets
    [BOM_Arduino_Spot_Welder_V2.2.xlsx]
2017-06-09 removed R13
    [Arduino_Board_Only_Spot_Welder-B.Cu.gbr, Arduino_Board_Only_Spot_Welder-B.Mask.gbr, Arduino_Board_Only_Spot_Welder-B.SilkS.gbr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]
2017-06-09 changed mosfets to IRFB7437
    [Mosfet_Board_Only_Spot_Welder-B.Cu.gbr, Mosfet_Board_Only_Spot_Welder-B.Mask.gbr, Mosfet_Board_Only_Spot_Welder-B.SilkS.gbr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]
2017-07-16 Changed R15 to 470 Ohm
    [BOM_Arduino_Spot_Welder_V2.2.xlsx]
